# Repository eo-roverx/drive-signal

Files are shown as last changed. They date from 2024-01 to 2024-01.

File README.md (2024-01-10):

# Drive Signal Breakout PCB Designs

Breaks out the drive signals from the STM32 to the motor drivers and encoders. Also includes headers for an IMU and the main SBC. It has the following features:

*   Connectors for 4 motors and encoders
*   LEDs for each motor (based on PWM)
*   Accepts 5V power on either USB or JST
*   Optional pull-up resistors for I2C

## Components

*   1x STM32F411CEU6 Microcontroller
*   4x 3-pin JST connectors for motor drivers
*   4x 4-pin JST connectors for motor encoders
*   1x 4-pin JST connector for IMU (I2C and 5V power) + direct female header
*   1x 3-pin JST connector for SBC (I2C)
*   1x 2-pin JST connector for 5V power
*   4x 4.7k 0805 SMD resistors (optional pull-ups for I2C)
*   4x 0805 SMD LEDs (optional motor status indicators)
*   4x 0805 SMD 2k resistors (current limiting for LEDs)
*   1x 0805 capacitor (optional for STM32 power filtering)
*   2x 3-pin JST connectors for additional I2C

## STM32 Pinouts

[STM32F411 Reference Page](https://stm32-base.org/boards/STM32F411CEU6-WeAct-Black-Pill-V2.0)

STM32F411 Reference Pinout

### Motor Driver

| STM32 Pin | Motor (Old Name) | MD30 Pin |
| --- | --- | --- |
| B4 | M1 (LF) | PWM |
| B5 | M1 (LF) | DIR |
| B8 | M2 (LB) | PWM |
| B9 | M2 (LB) | DIR |
| A5 | M3 (RB) | PWM |
| A6 | M3 (RB) | DIR |
| A1 | M4 (RF) | PWM |
| A2 | M4 (RF) | DIR |

### Motor Encoder

| STM32 Pin | Motor (Old Name) | Encoder Pin |
| --- | --- | --- |
| B12 | M1 (LF) | B |
| B13 | M1 (LF) | A |
| B14 | M2 (LB) | B |
| B15 | M2 (LB) | A |
| A3 | M3 (RB) | B |
| A4 | M3 (RB) | A |
| C14 | M4 (RF) | B |
| C15 | M4 (RF) | A |

### I2C

| STM32 Pin | Device | I2C Pin |
| --- | --- | --- |
| B6 | IMU | SCL (1) |
| B7 | IMU | SDA (1) |
| B10 | Jetson | SCL (2) |
| B3 | Jetson | SDA (2) |

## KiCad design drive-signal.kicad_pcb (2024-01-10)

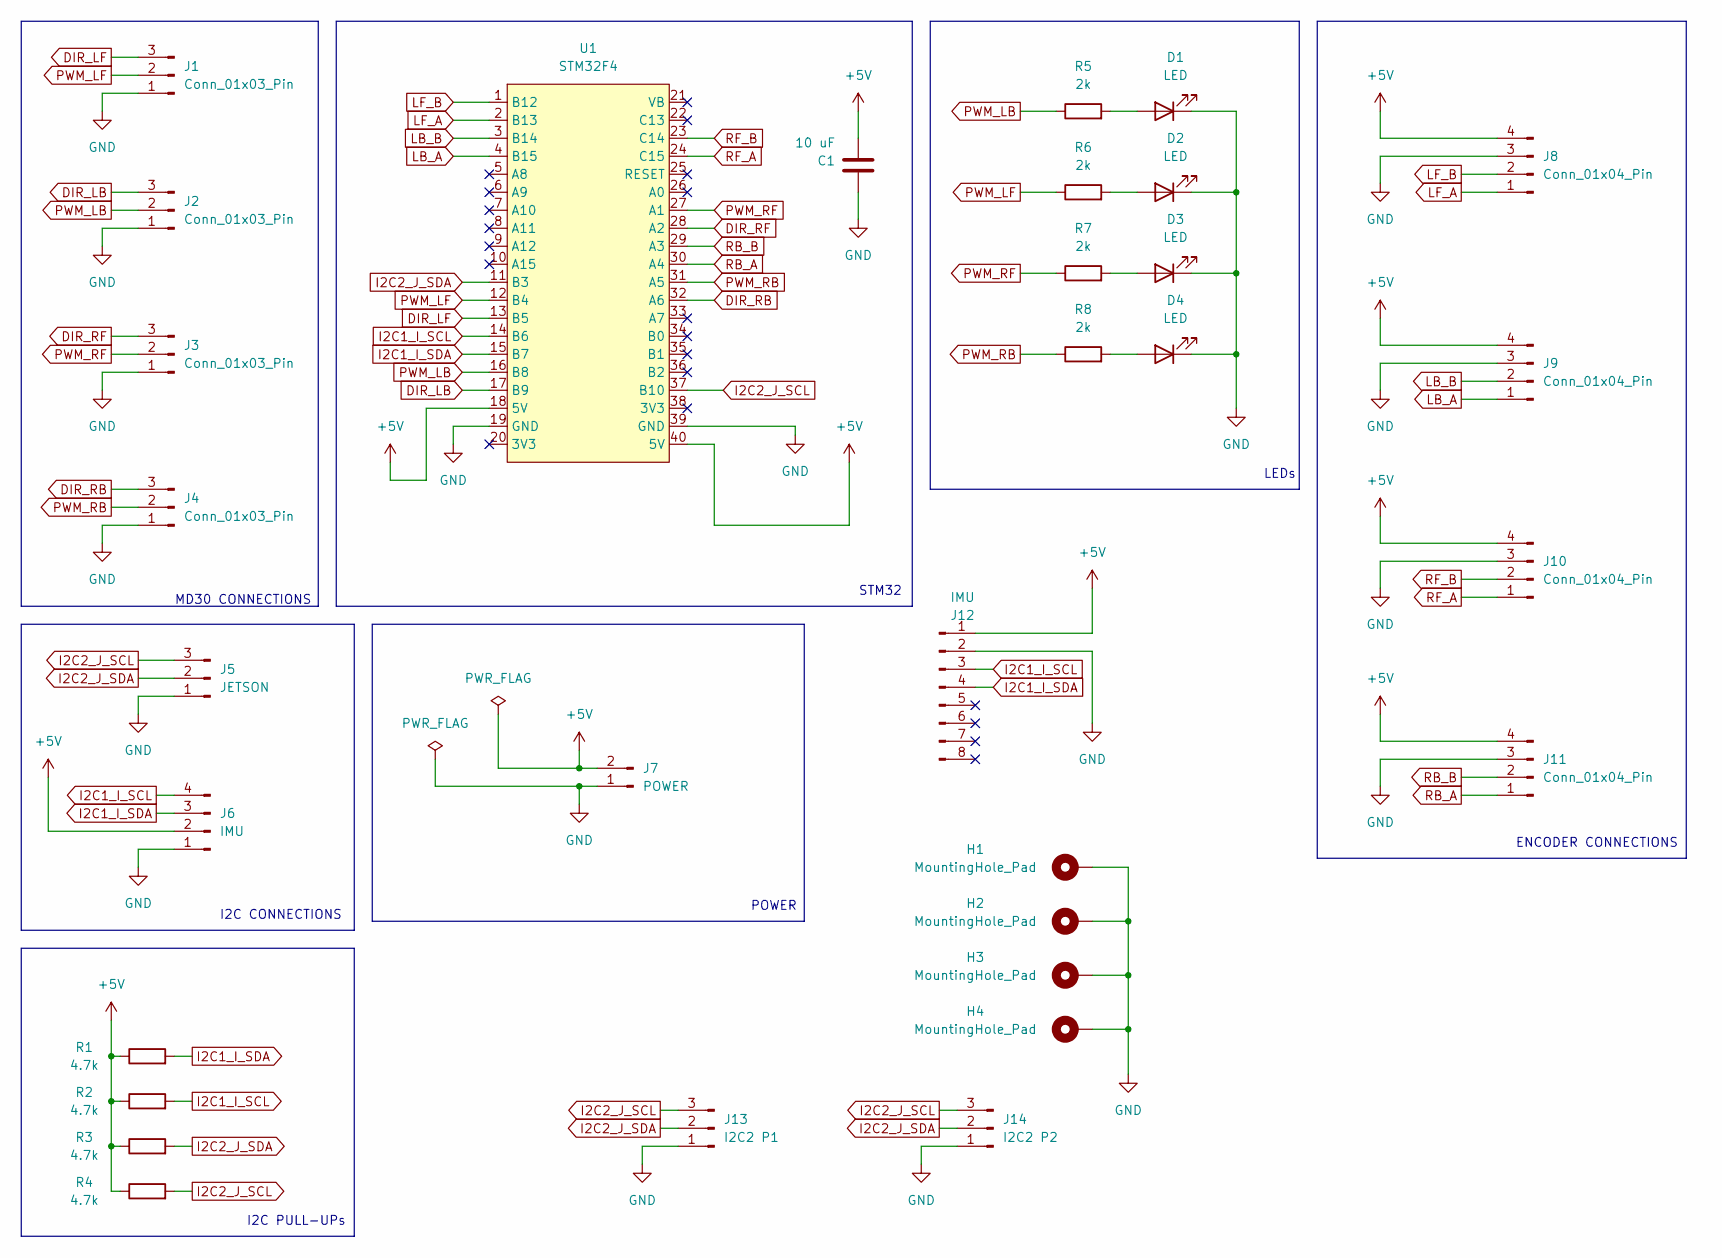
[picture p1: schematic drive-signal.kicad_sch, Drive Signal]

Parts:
C1: 10 uF; C_0805_2012Metric_Pad1.18x1.45mm_HandSolder
D1, D2, D3, D4: LED; LED_0805_2012Metric_Pad1.15x1.40mm_HandSolder
H1, H2, H3, H4: MountingHole_Pad; MountingHole_3.2mm_M3_Pad_Via
J1, J2, J3, J4: Conn_01x03_Pin; JST_EH_S3B-EH_1x03_P2.50mm_Horizontal
J5: JETSON; JST_EH_B3B-EH-A_1x03_P2.50mm_Vertical
J6: IMU; JST_EH_B4B-EH-A_1x04_P2.50mm_Vertical
J7: POWER; JST_EH_B2B-EH-A_1x02_P2.50mm_Vertical
J8, J9, J10, J11: Conn_01x04_Pin; JST_EH_S4B-EH_1x04_P2.50mm_Horizontal
J12: IMU; PinHeader_1x08_P2.54mm_Vertical
J13: I2C2 P1; JST_EH_S3B-EH_1x03_P2.50mm_Horizontal
J14: I2C2 P2; JST_EH_S3B-EH_1x03_P2.50mm_Horizontal
R1, R2, R3, R4: 4.7k; R_0805_2012Metric_Pad1.20x1.40mm_HandSolder
R5, R6, R7, R8: 2k; R_0805_2012Metric_Pad1.20x1.40mm_HandSolder
U1: STM32F4; STM32-BREAKOUT

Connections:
+5V: C1.1, J6.2, J7.2, J8.4, J9.4, J10.4, J11.4, J12.1, R1.1, R2.1, R3.1, R4.1, U1.18 (5V), U1.40 (5V)
DIR_LB: J2.3, U1.17 (B9)
DIR_LF: J1.3, U1.13 (B5)
DIR_RB: J4.3, U1.32 (A6)
DIR_RF: J3.3, U1.28 (A2)
GND: C1.2, D1.1 (K), D2.1 (K), D3.1 (K), D4.1 (K), H1.1, H2.1, H3.1, H4.1, J1.1, J2.1, J3.1, J4.1, J5.1, J6.1, J7.1, J8.3, J9.3, J10.3, J11.3, J12.2, J13.1, J14.1, U1.19 (GND), U1.39 (GND)
I2C1_I_SCL: J6.4, J12.3, R2.2, U1.14 (B6)
I2C1_I_SDA: J6.3, J12.4, R1.2, U1.15 (B7)
I2C2_J_SCL: J5.3, J13.3, J14.3, R4.2, U1.37 (B10)
I2C2_J_SDA: J5.2, J13.2, J14.2, R3.2, U1.11 (B3)
LB_A: J9.1, U1.4 (B15)
LB_B: J9.2, U1.3 (B14)
LF_A: J8.1, U1.2 (B13)
LF_B: J8.2, U1.1 (B12)
unnamed: D1.2 (A), R5.2
unnamed: D2.2 (A), R6.2
unnamed: D3.2 (A), R7.2
unnamed: D4.2 (A), R8.2
PWM_LB: J2.2, R5.1, U1.16 (B8)
PWM_LF: J1.2, R6.1, U1.12 (B4)
PWM_RB: J4.2, R8.1, U1.31 (A5)
PWM_RF: J3.2, R7.1, U1.27 (A1)
RB_A: J11.1, U1.30 (A4)
RB_B: J11.2, U1.29 (A3)
RF_A: J10.1, U1.24 (C15)
RF_B: J10.2, U1.23 (C14)

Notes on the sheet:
STM32
LEDs
MD30 CONNECTIONS
I2C PULL-UPs
POWER
I2C CONNECTIONS
ENCODER CONNECTIONS

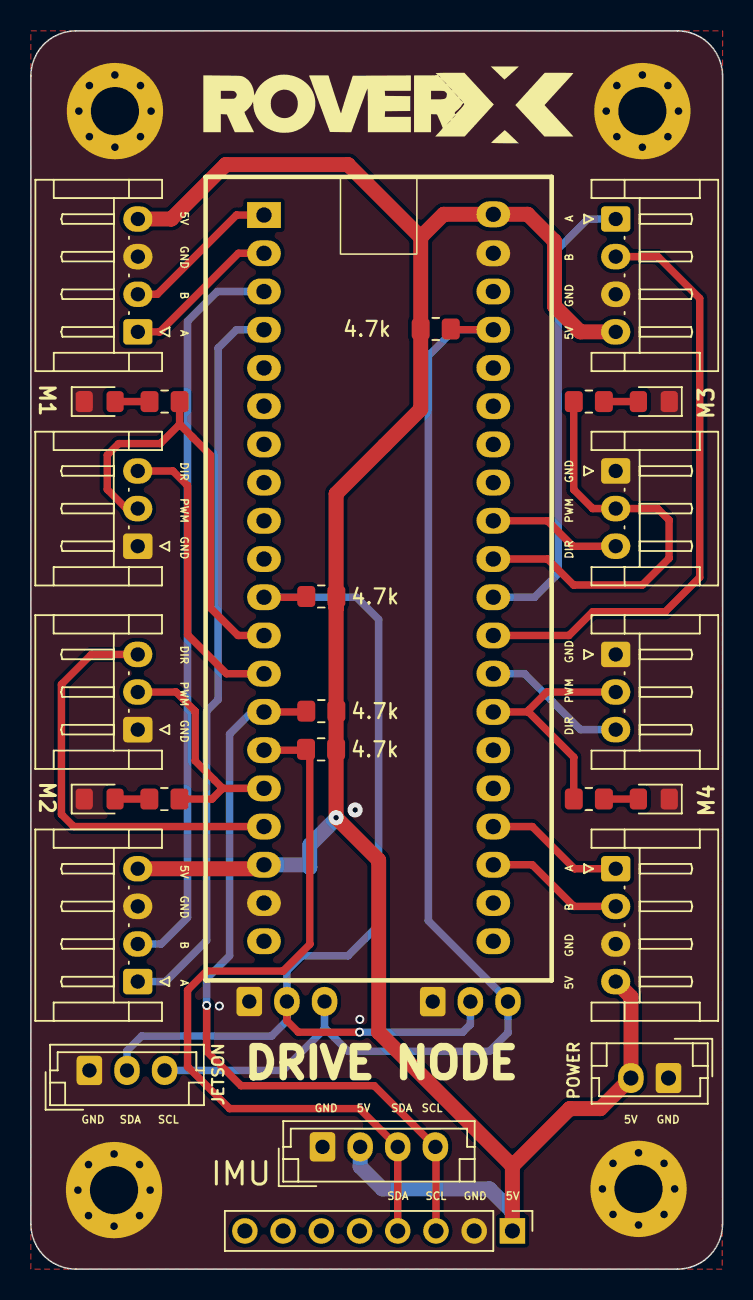
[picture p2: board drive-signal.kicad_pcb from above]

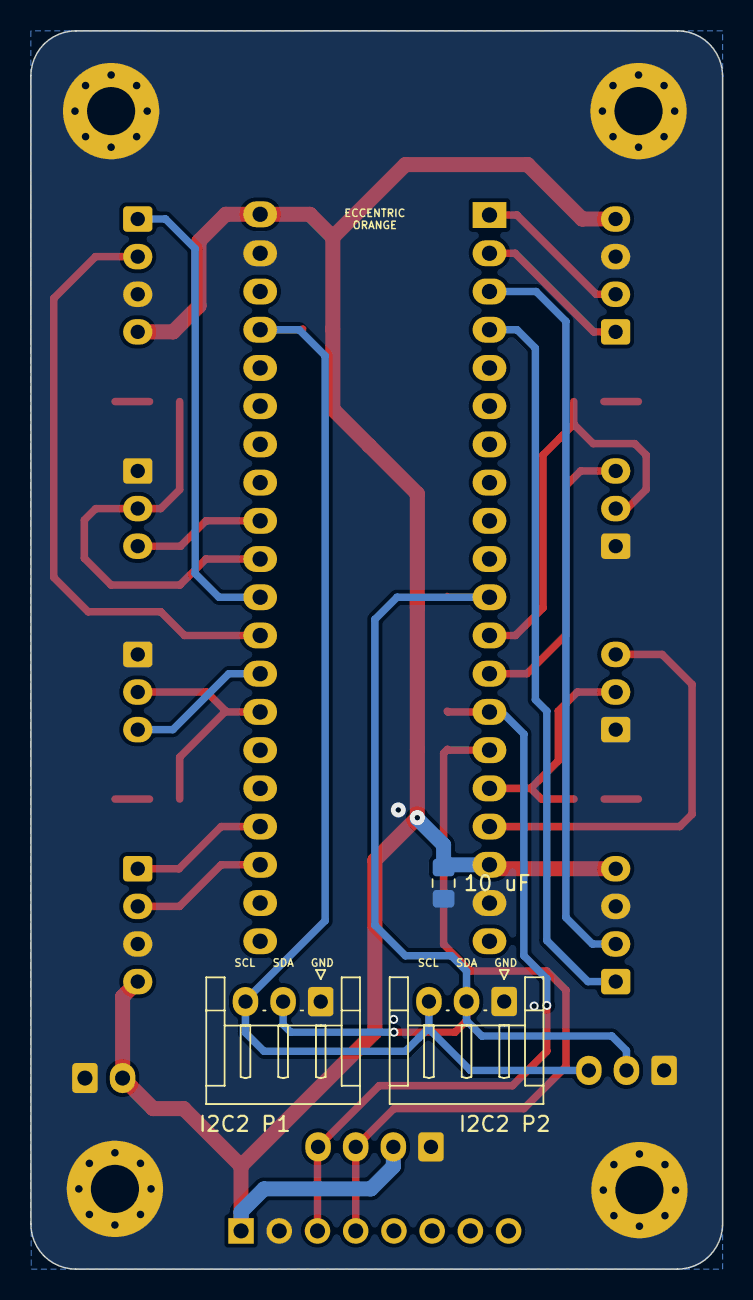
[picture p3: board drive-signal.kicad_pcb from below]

Board: 2 copper layers, 46.0 x 82.3 mm, 32 parts (3 on the bottom side), 26 nets.

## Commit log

2023-12-05 lay out basic PCB
    [drive-signal.kicad_pcb, drive-signal.kicad_sch]
2023-12-05 fix MD30 pinout
    [drive-signal.kicad_pcb, drive-signal.kicad_sch]
2023-12-05 incorporate feedback
    [drive-signal.kicad_pcb, drive-signal.kicad_sch]
2023-12-07 add gerbers
    [drive-signal.kicad_pcb]
2023-12-08 fix mount holes
    [drive-signal.kicad_pcb]
2023-12-26 make JSTs horizontal
    [drive-signal.kicad_pcb, drive-signal.kicad_sch]
2023-12-26 minor layout improvements
    [drive-signal.kicad_pcb]
2023-12-26 add mounting holes with pads
    [drive-signal.kicad_pcb, drive-signal.kicad_sch]
2023-12-26 reduce mounting holes
    [drive-signal.kicad_pcb, drive-signal.kicad_sch]
2024-01-09 done placement
    [drive-signal.kicad_pcb, drive-signal.kicad_sch]
2024-01-09 done something
    [drive-signal.kicad_pcb]
2024-01-10 vias and cleanup
    [drive-signal.kicad_pcb, drive-signal.kicad_sch]
